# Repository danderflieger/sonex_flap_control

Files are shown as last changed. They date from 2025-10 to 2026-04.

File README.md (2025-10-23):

# Sonex Flap Control
This is an experimental ameteur built (EAB) electronic project that was designed for flap movement and position tracking in my Sonex B model aircraft kit. It uses an Arduino Nano in conjunction with an BTS7960/IBT_2 H-type motor driver to move the Sonex-supplied Electric Flap Actuator (Sonex part SNB-C05-11) and displays current flap position on a small OLED screen. Feel free to use it for your own purposes AT YOUR OWN RISK. It is released under MIT open source agreement license (see the license agreement listed in the root of the project). 

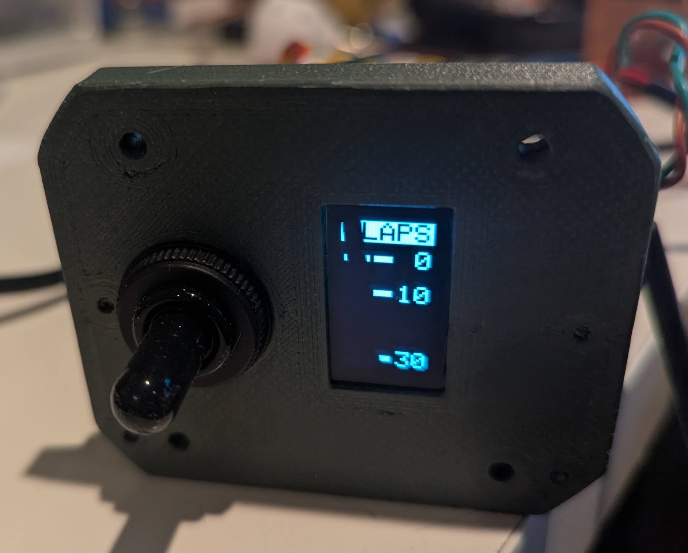
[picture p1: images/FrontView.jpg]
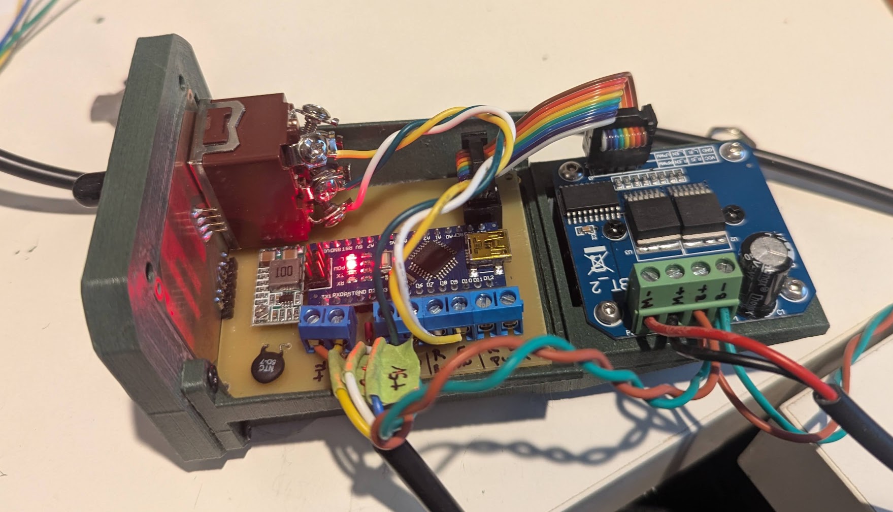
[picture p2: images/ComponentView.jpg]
  

Multiple "notches" can be configured in software. By default, I have added 3 notches - 0 degrees, 10 degrees, and 30 degrees. Pressing the switch upward on the face triggers the arduino to retract the flaps to the previous notch. Pressing down the switch triggers the flaps to extend to the next notch. If the user presses the opposite direction, the flaps stop. However, if the pilot flips the switch in the opposite direction and holds it for more than half a second, the flaps will stop for the half second and then reverse to the next notch. The OLED screen updates constantly to notify the pilot of the current flap position. So if a builder decided to wire the switch directly to the flap actuator, the OLED screen will still keep track of the current position of the flaps, but the pilot would need to hold the switch until the flaps extend/retract to the desired position.

The code has more comment blocks than actual code describing what is happening. Pretty much every line or function has a very detailed description of what it does and what to change (if anything).

For example, after building the device it will need to be calibrated to work with your individual flap actuator (e.g. position readings are likely to be close between your flap actuator and mine, but are unlikely to be __*exactly*__ the same as mine). There is a line of code that you will want to uncomment to view the position reading on the Serial Monitor when the flaps are fully retracted and fully extended (see example below). Those values need to be entered into the code so the device can be sure to reach its __*full range*__ with your actuator. All of that is described in comment blocks in the code. Here's a sample of my comment blocks within the Arduino code file:

```
...

/**************************************************************************
These two values represent the values recevied on the A2 pin of the Arduino,
which is connected to the yellow wire of the position sensor of the flap
actuator. To calibrate your actuator, set the CALIBRATION_OUTPUT to true
and find the sensor reading that appears when  you retract/extend the flap 
actuator to its limits in both directions. Use whatever value appears in
the Serial Monitor to set the FULL_RETRACT_VALUE and FULL_EXTEND_VALUE 
settings here. Then turn off the CALIBRATION_OUTPUT by setting it to false.
No need to continue to output values to the Serial port when it's not
necessary. 
**************************************************************************/
#define FULL_RETRACT_VALUE  5
#define FULL_EXTEND_VALUE   881

/**************************************************************************
 Decide whether or not to output serial data and/or calibration data over
 the serial port (e.g. through the Arduino IDE's Serial Monitor). The 
 SERIAL_OUTPUT switch will output lots of (possibly) useful data. 
 
 If CALIBRATION_OUTPUT is set to true, it will output readings so you can 
 adjust the two values above to match the flap acutator's readings when
 it's extended/retracted fully. 
 
 It's recommended that you set the FULL_RETRACT_VALUE to 0 and the 
 FULL_EXTEND_VALUE value to 1023 to start. Then set the CALIBRATION_OUTPUT 
 value to true and retract the actuator all the way.

 The output in the Serial Monitor will tell you what to put into the 
 FULL_RETRACT_VALUE. Then extend it all the way to figure out what the 
 FULL_EXTEND_VALUE should be set to. 
**************************************************************************/
#define SERIAL_OUTPUT       false
#define CALIBRATION_OUTPUT  false

...

```

The entire code base looks similar to this, with explainations for everything that's going on. If you're not a developer, reading through the comments can help you cut your teeth on Arduino C++ coding. 

# Parts/Supplies List
Here's a list of the parts I used while prototyping. You can probably find other vendors, but your mileage will likely vary. 
### Free-standing parts
  * __Sonex Electric Flap Actuator__
The Electric Flap Actuator requires a feedback circuit. Not all Sonex Electric Flap Actuators had the feedback circuit. To verify that yours has one, you will need to look at the two sets of wires coming out of the actuator. One of them will have a red and black wire - this is for 12-24V power. The other set of wires will have three leads - blue, white, and yellow. 
  * __Arduino Nano__ (https://www.amazon.com/dp/B07G99NNXL)
  * __BTS7960/IBT_2 H-Bridge DC Motor Driver__ (https://www.amazon.com/dp/B099N8XS5P)
  * __.96 inch OLED I2C Display Module - 128x64 pixels__ (https://www.amazon.com/dp/B09T6SJBV5)
  * __Marine-grade heavy duty 12V ON-OFF-ON momentary toggle switch__ (https://www.amazon.com/dp/B0F9P9L9G6)

### PCB-related Parts
Custom Printed Cirtuit Boards are required for this project. For the prototype, I used my ancient Canon laser printer to print a mirrored image on special paper, an iron to transfer the toner to a blank single-sided 
  * __FR-4 Copper Clad PCB Laminate, Single Side, 4x2.7 inch__ (https://www.amazon.com/dp/B01MCVLDDZ)
  * __Voltage Reducer/Buck Converter (set to 9V output)__ (https://www.amazon.com/dp/B08JZ5FVLC)
  * __PCB Screw Terminal Blocks__ (https://www.amazon.com/dp/B014GMRBH2) 
  * __Straight AND Right Angle 2.54mm Male Header Pins__ (https://www.amazon.com/dp/B0CN14TP2T)
  * __2x4 8P 2.54mm Straight Male Shrouded PCB Box Header IDC Socket__ (https://www.amazon.com/dp/B08DYFQKB1)

The Socket makes connecting the custom PCB to the motor driver board very simple and clean. You have two choices for the cable - you can buy the components and make your own custom cable (which is what I did) or you can purchase one already complete. I opted to make my own because the pre-made ones are a little too long and I didn't like that. 
  * __(pre-made) 2x4 Ribbon Cable__ (https://www.amazon.com/dp/B07DFBPZLJ)
  * __(custom) 2x4 FC-8P 2.54mm Dual Rows IDC Sockets Female Connector for Flat Ribbon Cable__ (https://www.amazon.com/dp/B0BVHMTY5S)
  * __(custom) Flat Ribbon Cable for 2.54mm 0.1" Spacing Connectors__ (https://www.amazon.com/dp/B0762ZCRYN)

### Other Recommended Parts
  * __Ferrule Crimping Tool and Connectors - crimp ends of wires to reduce fatigue__ (https://www.amazon.com/dp/B0DRJ9CDNG)
  * __22 AWG Stranded Tinned Copper Wire with Silicone Insulation__ (https://www.amazon.com/dp/B0881HCN37)

# Wiring
There are two sets of wires coming out of the Electronic Flap Actuator. One set is for powering the motion of the Actuator and the other set is for reporting its position.

### Power Wires

While the actuator has a red and a black wire coming out of it for motion, they won't always be positive/negative. If you give the red wire +12V and the black wire -12V, it will extend. If you reverse the polarity (+12V to black and -12V to red) the actuator will retract:
  * 🔴 RED:   Power (+ to extend, - to retract)
  * ⚫ BLACK: Power (- to extend, + to retract)

That said, there are two options for how to wire up the power to the actuator:

* You can wire the actuator to directly use 12/24V with a 6-pole, ON-OFF-ON momentary switch wired up like this (I got this diagram from an email sent to me by Sonex Support). This requires the pilot to press and hold the switch until the flaps reach the desired position:

  

* -OR- You can use the motor driver to change the polarity of the actuator for you. In this case, the motor controller is controlled by the Arduino and programmed to move the actuator in notches - so the pilot just flips and releases the switch in the direction the flaps should go for literally a few milliseconds - no need to hold it - and then goes back to flying the airplane while the flaps move to the desired position with no additional input required from the pilot.

Both of these options will work with the indicator, requiring no change to the code. The Arduino will listen for switch input, but if no pilot input is received, it just merrily skips to the position reading and diplays it on the little screen. 

#### Motor Driver Use Discussion
The motor driver has several inputs and two outputs. The two outputs are the red and black wires on the actuator. The motor driver will determine how much voltage (and which polarity - remember we need to reverse the polarity to the actuator for retraction) to push to the actuator based on the other pins. Here's a list of the other pins and what they do:

* __M-__ - Output to the Actuator (this will output positive or negative power, depending on which way the actuator should move)
* __M+__ - Other output to the Actuator (this will output negative or positive power, depending on which way the actuator should move)
* __B-__ - This is the max negative power source/ground of the airplane 
* __B+__ - This is the max positive power (e.g. +12V from the battery) that can be pushed to the actuator. The Motor Driver can handle up to 36V, but I suggest just using the common 12V or 24V.
* __VCC__ - This is 5V provided by the Arduino. It's only used to power the LOGIC of the motor driver (not the motor itself)
* __GND__ - This is a common ground between the Arduino and the Motor Driver
* __R_IS__ and __L_IS__ - These two pins are not used in this project - I think they're for re-programming the motor driver or something like that. Just ignore them.
* __R_EN__ and __L_EN__ - These two pins are given 5V, which "enables" the two BTS7960 chips (one is on the right and one is on the left). If these pins are not "enabled" with 5V, the motor driver won't send any power to the Actuator
* __RPWM__ and __LPWM__ - These two pins are controlled by the Arduino - one for each BTS7960 chip on the Motor Driver board. Depending on the PWM signal from the arduino on either of these two pins, the motor driver will send a variable voltage to the actuator. To extend, we give a high PWM to the RPWM pin and NO signal to the LPWM pin. To retract, we give a high PWM signal to the LPWM pin and NO signal to the RPWM pin. see below for a description of PWM.

#### PWM Discussion
Pulse Width Modulation (PWM) is determined by turning a signal pin on and off at varying rates. Arduinos are designed to do this on their digital pins. We can set a PWM value between 0 and 255 on any Arduino digital pin. A PWM cycle is the amount of time in which a pin goes from on to off. Each PWM cycle on a typical Arduino (such as the Nano used in the project), that cycle is about every 2 milliseconds. 

A PWM value of 0 denotes that the pin is always outputting 0V. A PWM of 255 denotes that the pin
is always outputting 5V. 

A PWM output of 127 means that a pin is on (5V) for about 1ms and off (0V) for about 1ms. 

A PWM of 63 (half of 127) means that the pin will be turned on (5V) for 500 micro seconds (half of a millisecond) and off (0V) for 1500 microseconds (1.5 milliseconds). Or in other words, for about 1/4 of the cycle the pin will be outputting 5V and the other 3/4 of the cycle it will be outputting 0V.

To tell the Motor Driver to move the actuator in one direction or the other, you need to send two PWM signals - one to each of the BTS7960 chips. 

To extend the actuator, we would send a PWM of 0 to the RPWM pin and a PWM of 255 to the LPWM pin on the motor driver. This will cause the output terminal to push +12V to the red wire and -12V to the black wire on the actuator. 

To retract the actuator, we do the opposite. E.g. send a PWM of 0 to the LPWM pin and a PWM of 255 to the RPWM pin on the driver. This will revers the polarity to the actuator +12V on the BLACK wire and -12V on the RED wire. 

To slow down the motion of actuator, you would set your PWM signal at a low number - say 10. 

To speed up the movement of the actuator, you would increase the PWM to something higher - 1 to 255. 

There's a good write-up on Arduino's website about PWM - it's worth reading:
https://docs.arduino.cc/learn/microcontrollers/analog-output/ 

Note: For this project, there's no danger in just telling the motor controller to move in one direction at full speed until it reaches it's desired flap position. The actuator moves slowly enough to not worry about overshooting your flap setting by very much - I've added an additional threshold variable to account for the actuator "coasting" momentarily after telling it to stop. If set properly, this threshold will stop the actuator exactly where you want it to stop.

Now, on to the other set of wires coming out of the Electronic Flap Actuator ...

### Position Sensor Wires

The real benefit to this project is the flap position indicator. You can use the built-in position sensor to display the position of the flaps on your panel.

  * 🔵 BLUE: +5V
  * ⚪ WHITE: -5V/Ground
  * 🟡 YELLOW: 0 to +5V Signal wire (read by analog pin A2 on Arduino)

Every time the Arduino loops through the aptly named loop() function, it checks to see if there's any input from the pilot (if so, it tries to do what the pilot told it to do) and it also takes a reading from the sensor wires and updates the OLED screen with the new reading. This happens hundreds of times per second and gives near instant updates on the little screen. 

#### How the position sensor works
The position sensor is fed +5V on the blue wire and -5V on the white wire. There's a potentiometer in between with an output (yellow wire) that will output anywhere from 0V (if fully retracted) to +5V (if fully extended). If it's roughly halfway between the two, the yellow wire will output about +2.5V. 

One of the Arduino's analog pins (in this case A2) is set up to listen to the amount of voltage coming through that yellow wire. It then translates that voltage to a number between 0 and 1023. In the code, we then use a "map()" function to interpolate the value from a min/max range that the pin can read (0-1023) to a range that makes sense from a "degrees of flaps" perspective (this is defined in the code 0-30, but can be eaily changed to something else). The map() function works like this:

```
map([value recevied from yellow wire - 0-1023], [min input value - e.g. fully retracted reading], [max input value - e.g. fully extended reading], [min flap angle as defined], [max flap angle as defined]); 
```

So, given that:

* our sensor is currently sending 2.5V to the Arduino, so the Arduino reads __511__ (half way between 0 and 1023)
* our min/max values that the sensor outputs (say 0 to +5V) is converted to a number between __0__ and __1023__
* our min/max angle settings are __0__ and __30__  

that means our map() function would look like this:

__flapAngle = map(511, 0, 1023, 0, 30);__

In this case, the flapAngle variable would be set to 15 degrees of flap (e.g. half way between 0 and 30, because the actuator's sensor is reporting that it's halfway between fully extended and fully retracted). 

Once we have that value, we use a handy little OLED library written by the folks at Adafruit to draw a little rectangle on the left half of the screen (showing graphically where the flaps are currently positioned) next to a previously drawn set of lines and numbers showing where certain values will appear on the screen (on the right). 

Incedentally, we use another map() function to convert the angle value we figured out a minute ago to determine where to place the little rectangle based on the number of pixels high the screen is, minus the text at the top that says FLAPS. Giving similar values, our map() function to find the vertical position of our rectangle would look like this (where the range of available pixels is 8 to 128):

rectangleTopLeftCorner = (15, 0, 30, 8, 128); 

So the rectangleTopLeftCorner variable would be set to 60 - which means the rectangle's top left corner would be drawn on the screen at 60 pixels from the top. map() is a very handy little function!

Anyway, that's a pretty good intro. For more details, go read the comment blocks in the code - I explain a lot more there.

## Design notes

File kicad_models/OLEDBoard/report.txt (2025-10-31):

Plotted to 'C:\Users\ripperuser\Documents\sonex_flap_control\kicad_models\ArduinoBoard\GerberFiles\ArduinoBoard-F_Cu.gbr'.
Plotted to 'C:\Users\ripperuser\Documents\sonex_flap_control\kicad_models\ArduinoBoard\GerberFiles\ArduinoBoard-B_Cu.gbr'.
Plotted to 'C:\Users\ripperuser\Documents\sonex_flap_control\kicad_models\ArduinoBoard\GerberFiles\ArduinoBoard-F_Paste.gbr'.
Plotted to 'C:\Users\ripperuser\Documents\sonex_flap_control\kicad_models\ArduinoBoard\GerberFiles\ArduinoBoard-B_Paste.gbr'.
Plotted to 'C:\Users\ripperuser\Documents\sonex_flap_control\kicad_models\ArduinoBoard\GerberFiles\ArduinoBoard-F_Silkscreen.gbr'.
Plotted to 'C:\Users\ripperuser\Documents\sonex_flap_control\kicad_models\ArduinoBoard\GerberFiles\ArduinoBoard-B_Silkscreen.gbr'.
Plotted to 'C:\Users\ripperuser\Documents\sonex_flap_control\kicad_models\ArduinoBoard\GerberFiles\ArduinoBoard-F_Mask.gbr'.
Plotted to 'C:\Users\ripperuser\Documents\sonex_flap_control\kicad_models\ArduinoBoard\GerberFiles\ArduinoBoard-B_Mask.gbr'.
Plotted to 'C:\Users\ripperuser\Documents\sonex_flap_control\kicad_models\ArduinoBoard\GerberFiles\ArduinoBoard-Edge_Cuts.gbr'.
Created Gerber job file 'C:\Users\ripperuser\Documents\sonex_flap_control\kicad_models\ArduinoBoard\GerberFiles\ArduinoBoard-job.gbrjob'.
Info: Done.
Plotted to 'C:\Users\ripperuser\Documents\sonex_flap_control\kicad_models\ArduinoBoard\GerberFiles\ArduinoBoard-F_Cu.gbr'.
Plotted to 'C:\Users\ripperuser\Documents\sonex_flap_control\kicad_models\ArduinoBoard\GerberFiles\ArduinoBoard-B_Cu.gbr'.
Plotted to 'C:\Users\ripperuser\Documents\sonex_flap_control\kicad_models\ArduinoBoard\GerberFiles\ArduinoBoard-F_Paste.gbr'.
Plotted to 'C:\Users\ripperuser\Documents\sonex_flap_control\kicad_models\ArduinoBoard\GerberFiles\ArduinoBoard-B_Paste.gbr'.
Plotted to 'C:\Users\ripperuser\Documents\sonex_flap_control\kicad_models\ArduinoBoard\GerberFiles\ArduinoBoard-F_Silkscreen.gbr'.
Plotted to 'C:\Users\ripperuser\Documents\sonex_flap_control\kicad_models\ArduinoBoard\GerberFiles\ArduinoBoard-B_Silkscreen.gbr'.
Plotted to 'C:\Users\ripperuser\Documents\sonex_flap_control\kicad_models\ArduinoBoard\GerberFiles\ArduinoBoard-F_Mask.gbr'.
Plotted to 'C:\Users\ripperuser\Documents\sonex_flap_control\kicad_models\ArduinoBoard\GerberFiles\ArduinoBoard-B_Mask.gbr'.
Plotted to 'C:\Users\ripperuser\Documents\sonex_flap_control\kicad_models\ArduinoBoard\GerberFiles\ArduinoBoard-Edge_Cuts.gbr'.
Created Gerber job file 'C:\Users\ripperuser\Documents\sonex_flap_control\kicad_models\ArduinoBoard\GerberFiles\ArduinoBoard-job.gbrjob'.
Info: Done.
Info: Done.
Info: Done.

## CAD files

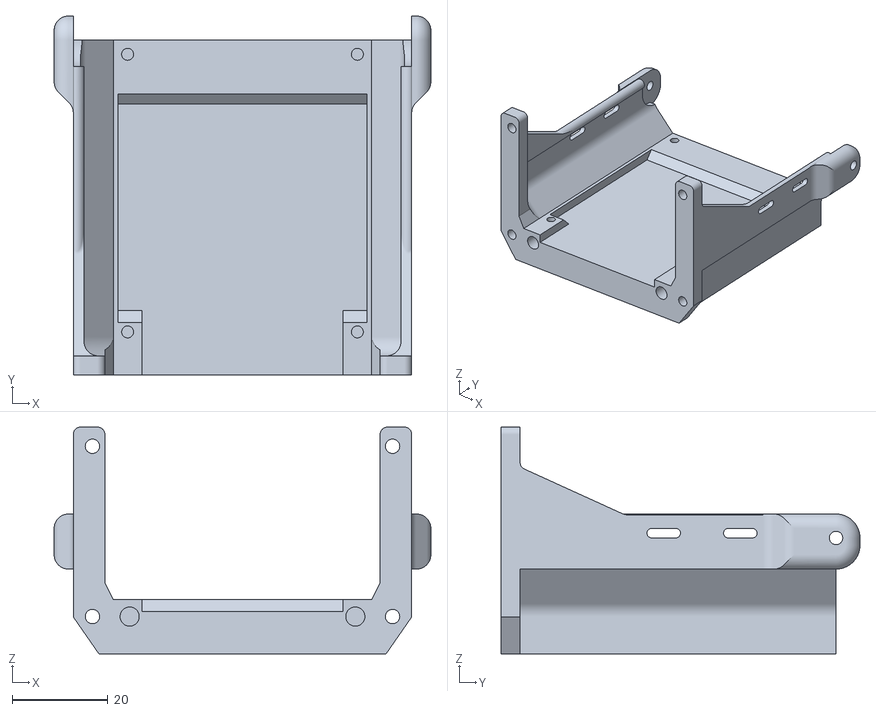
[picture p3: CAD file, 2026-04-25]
Solid Edge/STL Files/MainBoardBed.stl
78.7 x 75.0 x 47.4

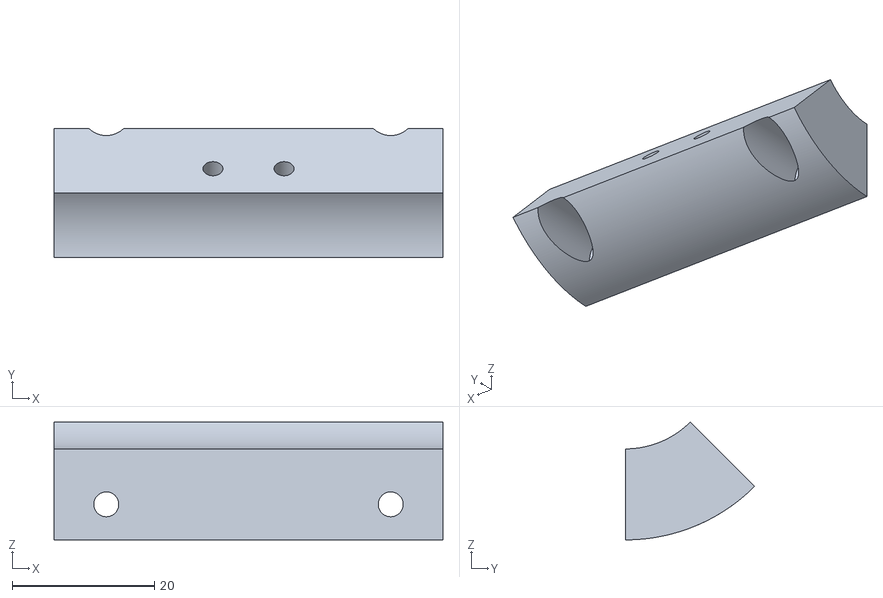
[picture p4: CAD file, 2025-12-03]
Solid Edge/STL Files/45DegMotorBoardBedSpacer.stl
54.7 x 18.1 x 16.6

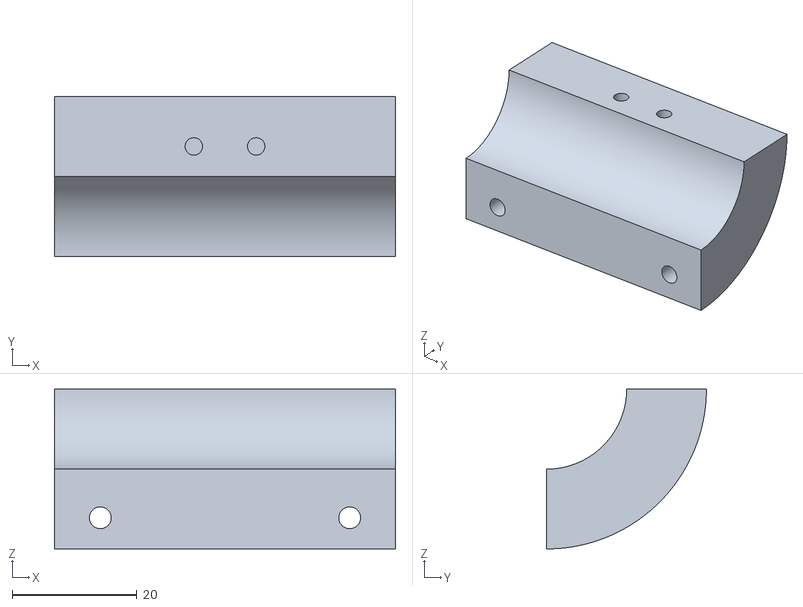
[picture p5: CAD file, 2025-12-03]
Solid Edge/STL Files/90DegMotorBoardBedSpacer.stl
54.7 x 25.6 x 25.6

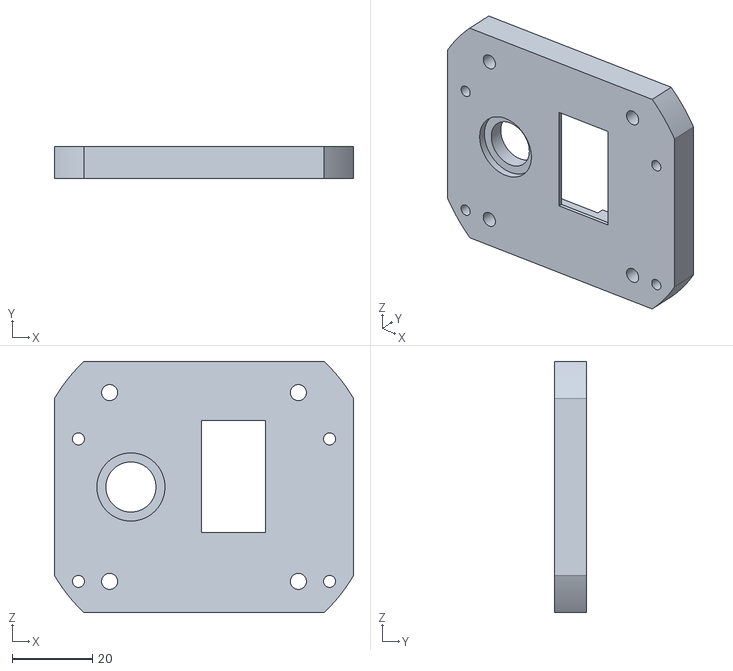
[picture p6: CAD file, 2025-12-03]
Solid Edge/STL Files/FacePlate.stl
74.7 x 8.00 x 62.7

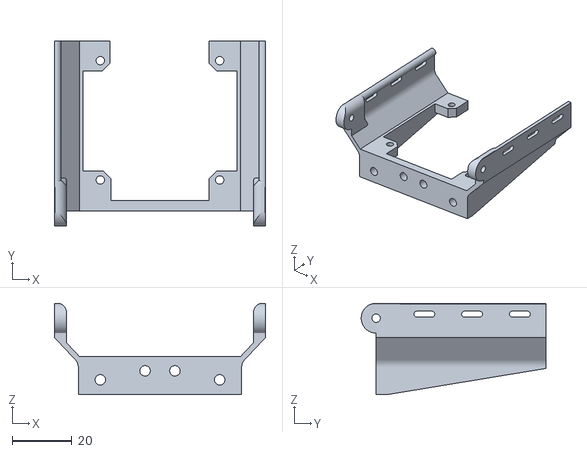
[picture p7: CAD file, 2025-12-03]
Solid Edge/STL Files/MotorDriverMount.stl
70.7 x 61.9 x 30.6

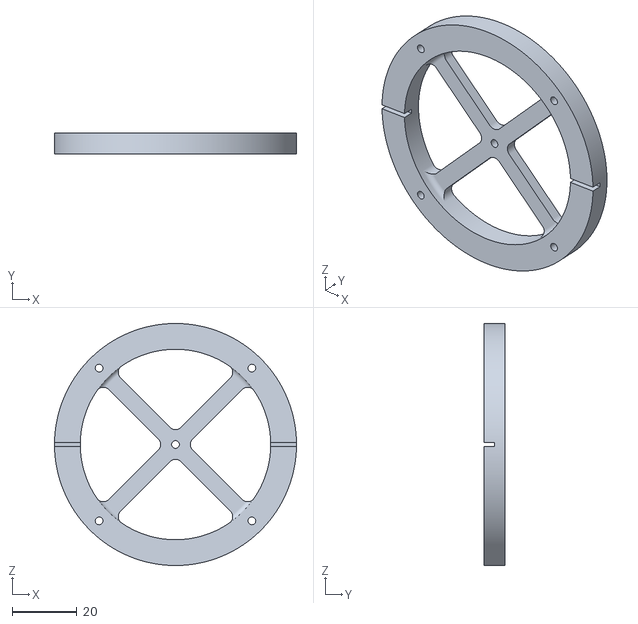
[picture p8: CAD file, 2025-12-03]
Solid Edge/STL Files/Panel Hole Template.stl
74.7 x 6.35 x 74.7

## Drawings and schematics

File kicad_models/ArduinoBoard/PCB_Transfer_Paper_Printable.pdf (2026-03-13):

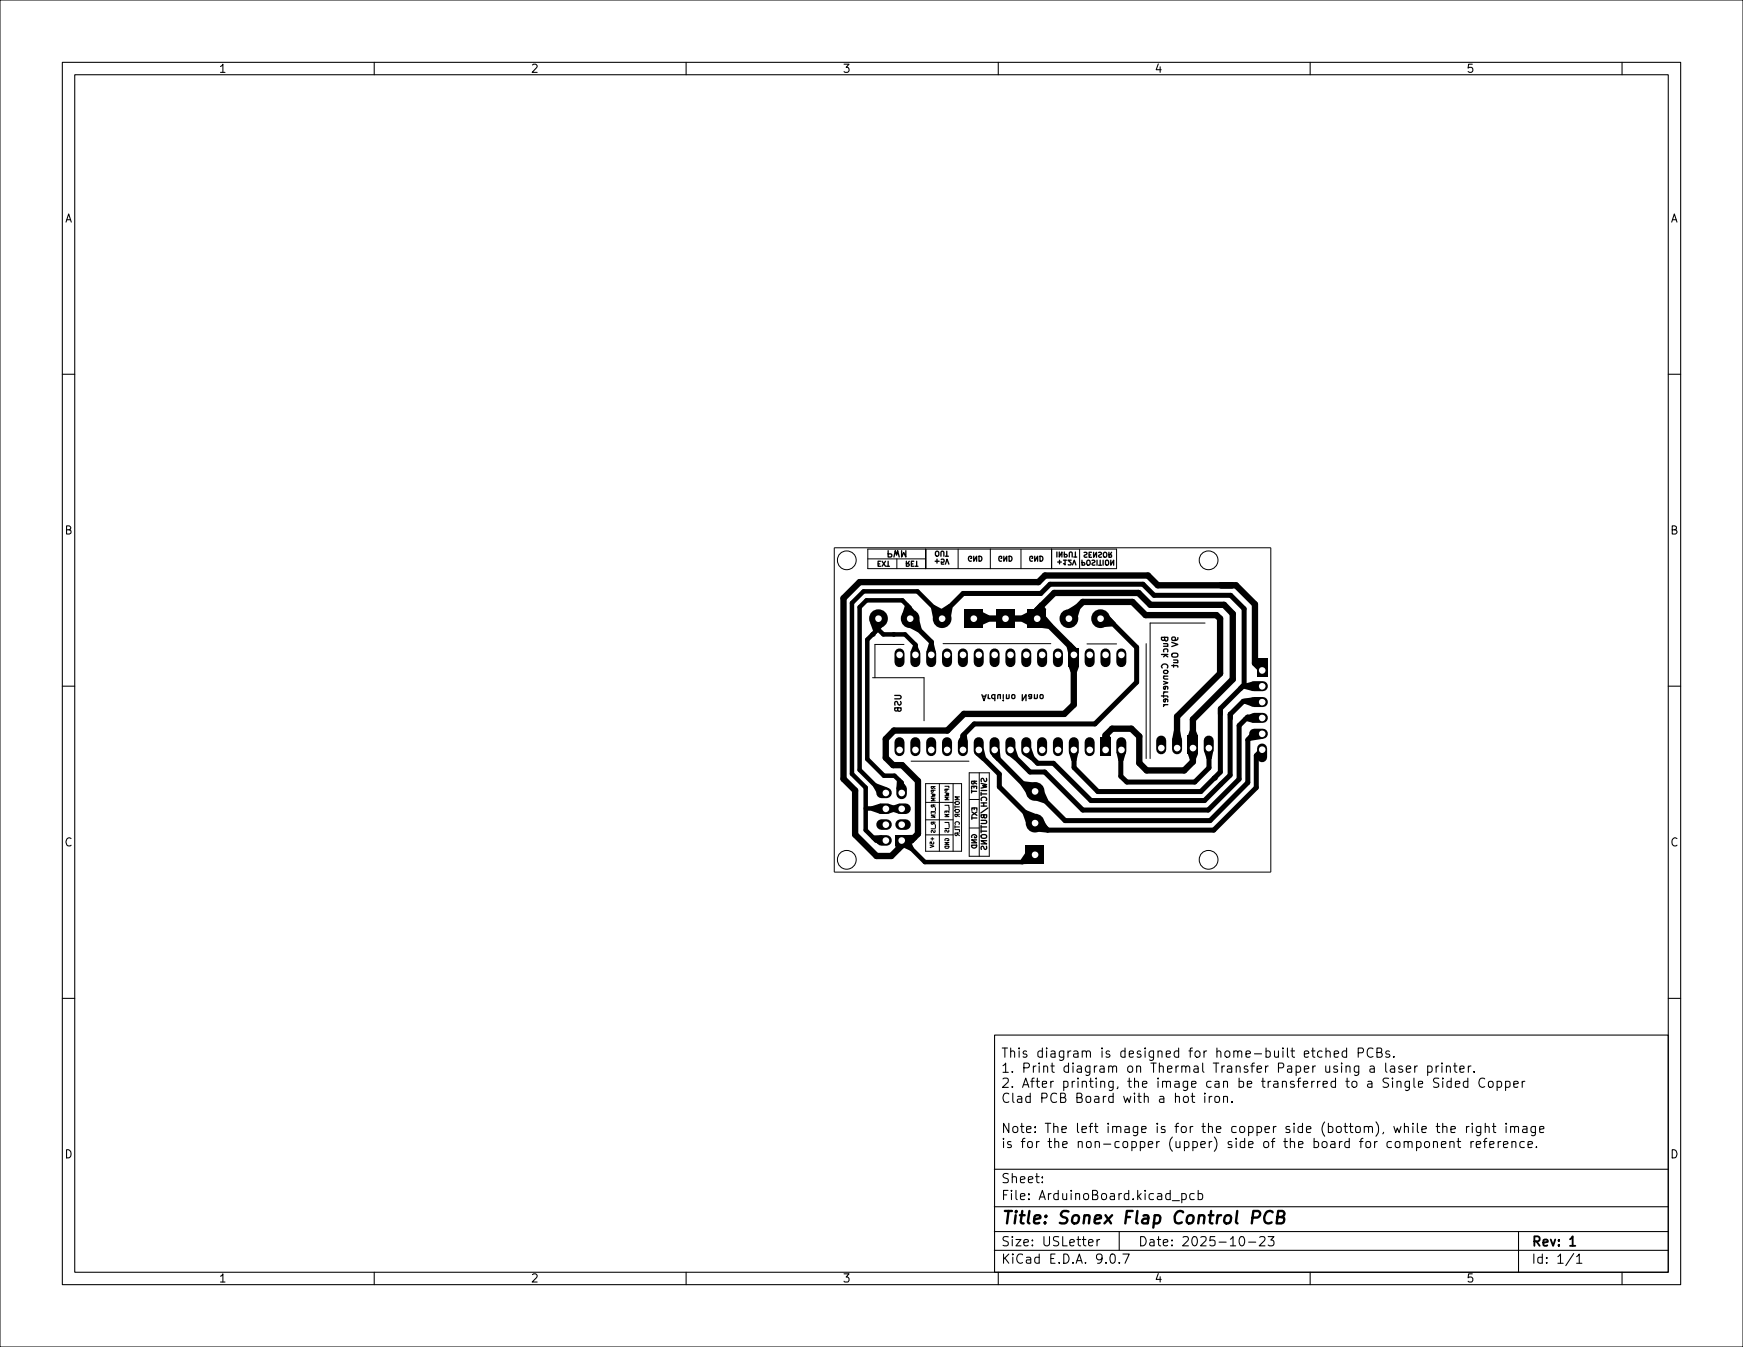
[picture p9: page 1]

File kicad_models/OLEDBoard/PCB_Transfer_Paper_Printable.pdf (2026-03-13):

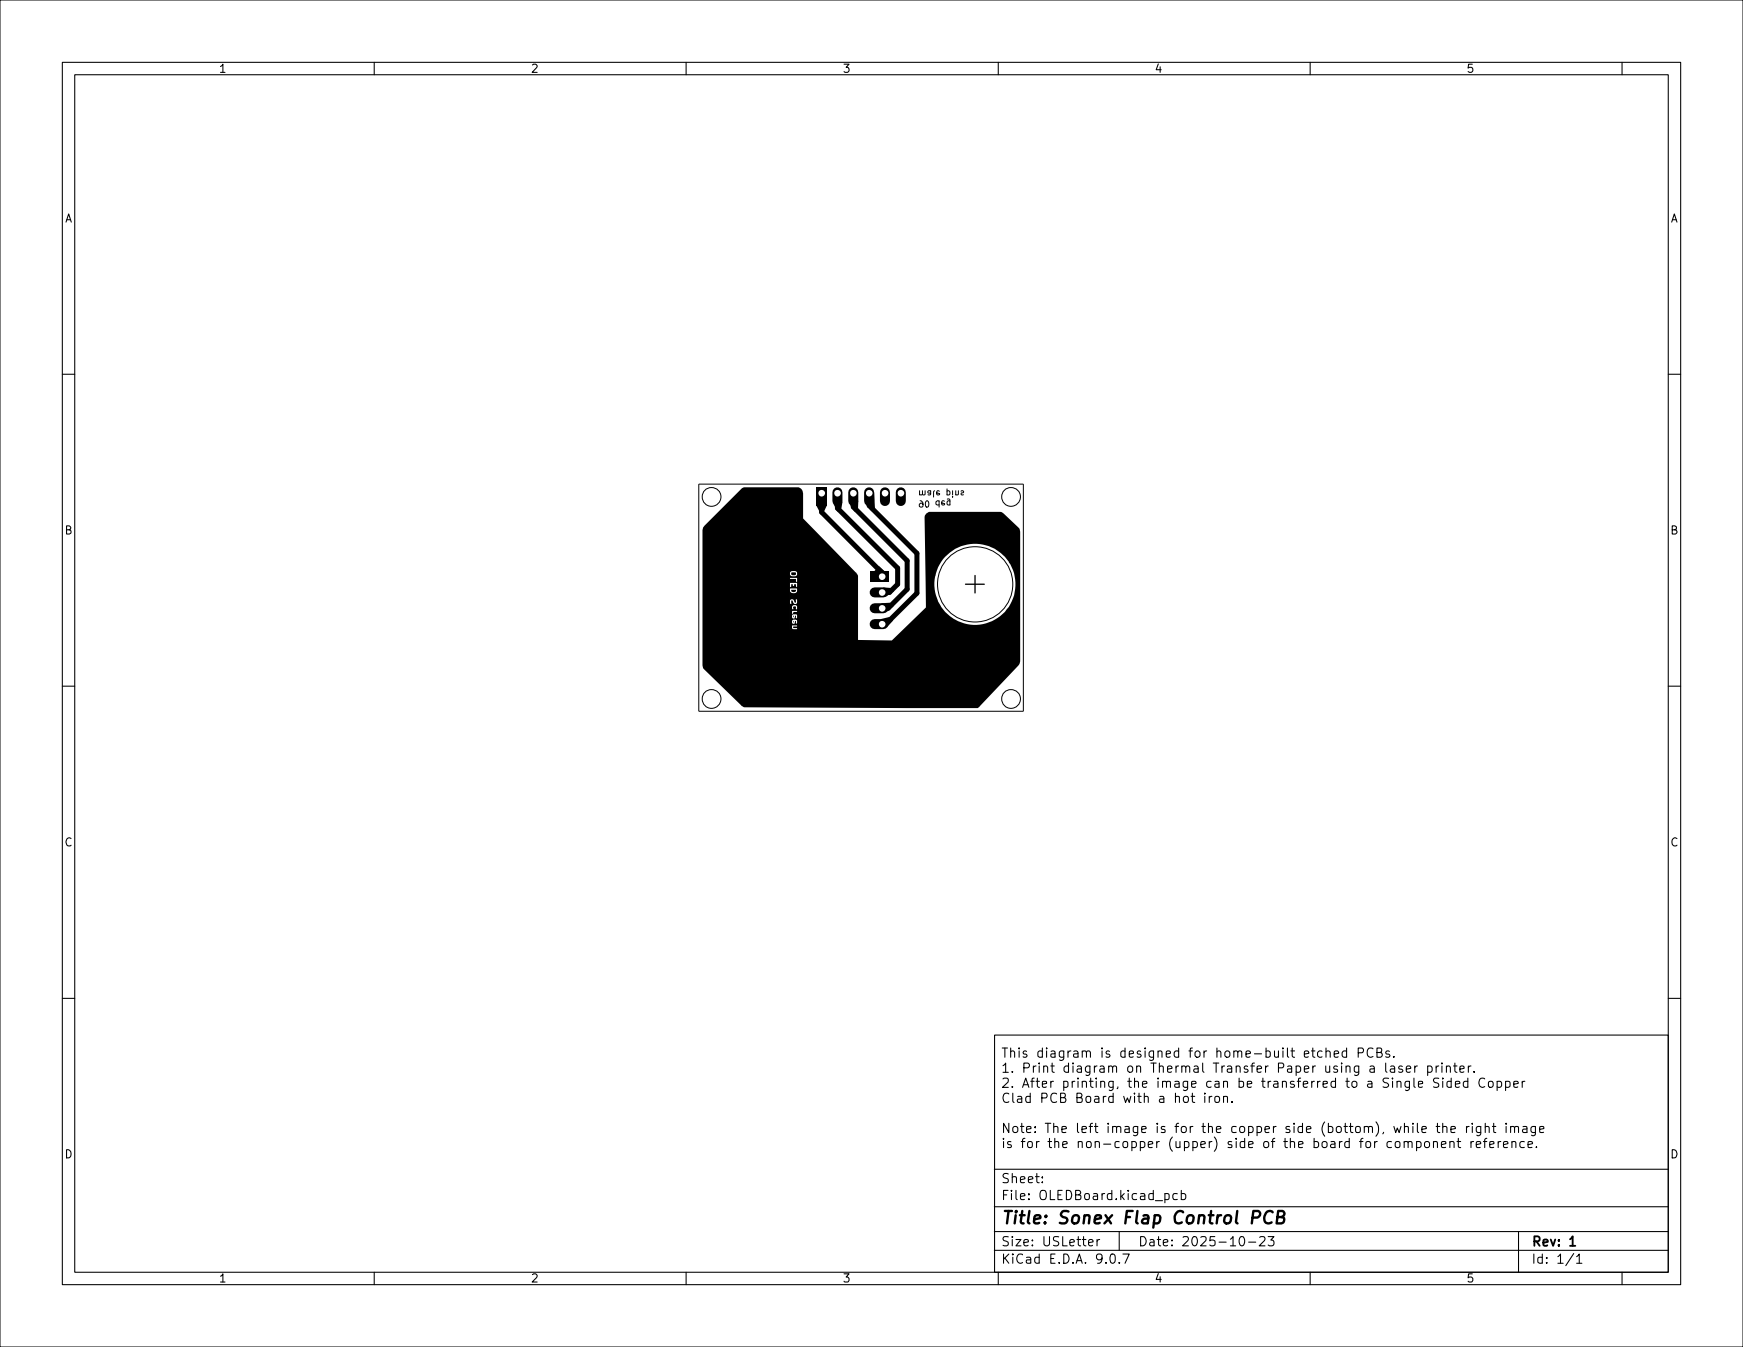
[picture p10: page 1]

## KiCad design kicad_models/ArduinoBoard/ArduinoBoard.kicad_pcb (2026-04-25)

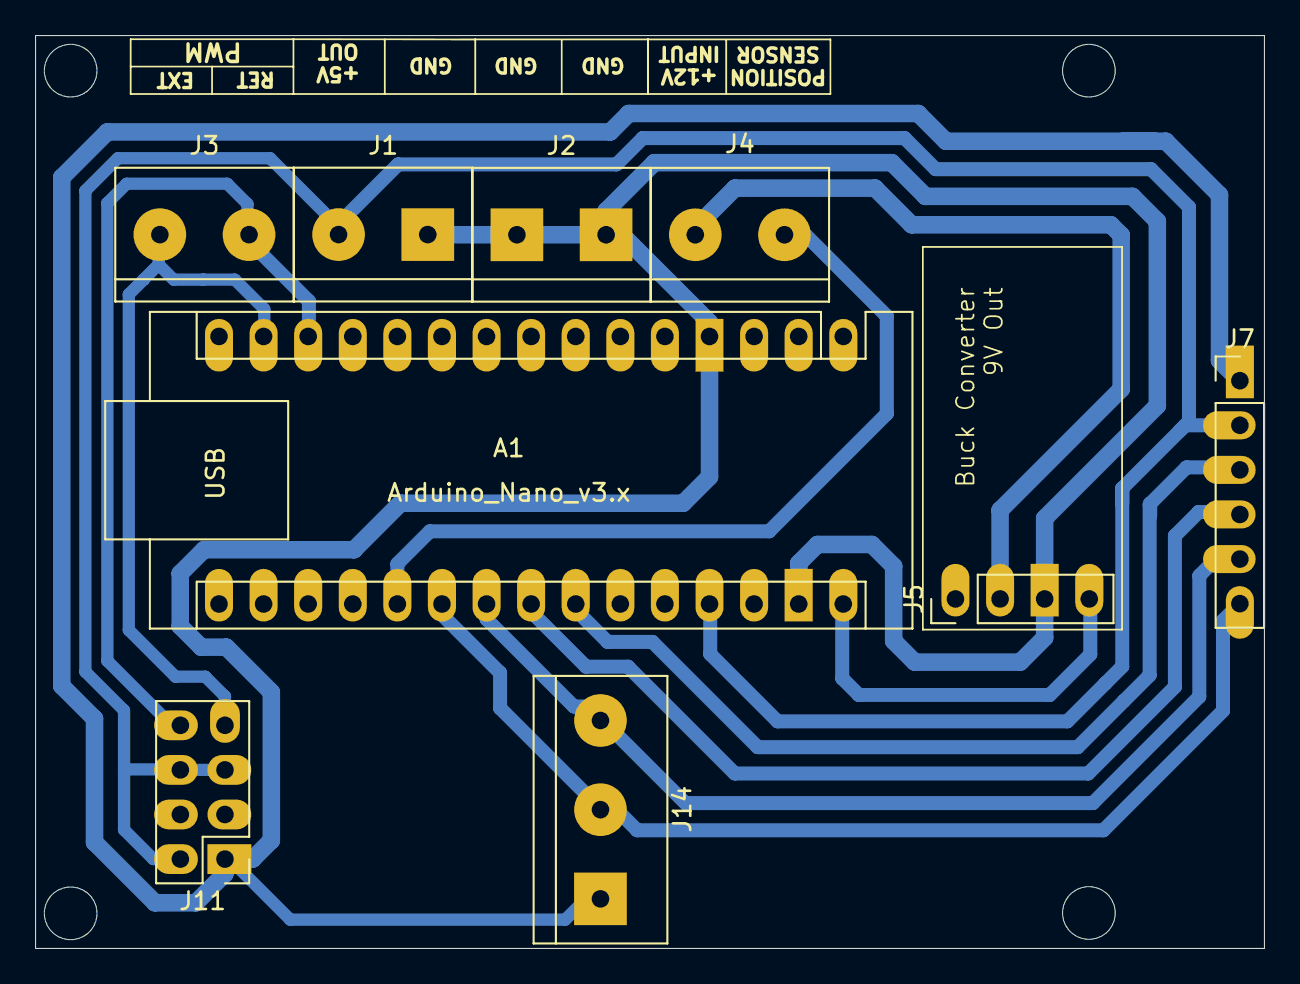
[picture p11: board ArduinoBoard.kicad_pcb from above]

Board: 2 copper layers, 70.0 x 52.0 mm, 9 parts (0 on the bottom side), 11 nets.

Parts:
A1: Arduino_Nano_v3.x; Arduino_Nano
J1, J2: 5V Output; TerminalBlock_bornier-2_P5.08mm
J3: PWM Output; TerminalBlock_bornier-2_P5.08mm
J4: 12V Input; TerminalBlock_bornier-2_P5.08mm
J5: Conn_01x04_Pin; PinHeader_1x04_P2.54mm_Vertical
J7: Conn_01x06_Pin; PinHeader_1x06_P2.54mm_Vertical
J11: Conn_02x04_Odd_Even; PinHeader_2x04_P2.54mm_Vertical
J14: Switch/Buttons; TerminalBlock_bornier-3_P5.08mm

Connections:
/GND: A1.4 (GND), A1.29 (GND), J1.2, J2.1, J2.2, J5.3, J7.1, J11.1, J14.3
/VI+: J4.1, J5.2
/VO+: A1.30 (VIN), J5.4
unnamed: A1.27 (+5V), J1.1, J7.2, J11.2, J11.5, J11.6
unnamed: A1.20 (A1), J4.2
unnamed: A1.21 (A2), J7.6, J14.2
unnamed: A1.22 (A3), J7.5, J14.1
unnamed: A1.23 (A4), J7.4
unnamed: A1.24 (A5), J7.3
unnamed: A1.13 (D10), J3.2, J11.8
unnamed: A1.14 (D11), J3.1, J11.7

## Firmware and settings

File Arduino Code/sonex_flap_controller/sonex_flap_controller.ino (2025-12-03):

/**************************************************************************
  MIT License

  Copyright (c) 2025 Dan Der Flieger

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
  THE SOFTWARE IS PROVIDED "AS IS", WITHOUT WARRANTY OF ANY KIND, EXPRESS OR
  IMPLIED, INCLUDING BUT NOT LIMITED TO THE WARRANTIES OF MERCHANTABILITY,
  FITNESS FOR A PARTICULAR PURPOSE AND NONINFRINGEMENT. IN NO EVENT SHALL THE
  AUTHORS OR COPYRIGHT HOLDERS BE LIABLE FOR ANY CLAIM, DAMAGES OR OTHER
  LIABILITY, WHETHER IN AN ACTION OF CONTRACT, TORT OR OTHERWISE, ARISING FROM,
  OUT OF OR IN CONNECTION WITH THE SOFTWARE OR THE USE OR OTHER DEALINGS IN THE
  SOFTWARE.
**************************************************************************/


/**************************************************************************
  Include a few necessary libraries - the Adafruit ones need to be installed
  into the Arduino IDE before this will compile. See the copyright info 
  for the Adafruit libraries at the bottom of this file. Basically, just 
  consider the time and money expended to write a freely available library
  and think about buying their hardware (which is top-notch). 
**************************************************************************/
#include <SPI.h>
#include <Wire.h>
#include <Adafruit_GFX.h>
#include <Adafruit_SSD1306.h>


/**************************************************************************
These two values represent the values recevied on the READING_PIN pin of the 
Arduino, which is connected to the yellow wire of the position sensor of the 
flap actuator. To calibrate your actuator, set the CALIBRATION_OUTPUT to 
true and find the sensor reading that appears when  you retract/extend the 
flap actuator to its limits in both directions. Use whatever value appears 
in the Serial Monitor to set the FULL_RETRACT_VALUE and FULL_EXTEND_VALUE 
settings here. Then turn off the CALIBRATION_OUTPUT by setting it to false.
No need to continue to output values to the Serial port when it's not
necessary. 
**************************************************************************/
#define FULL_RETRACT_VALUE  6
#define FULL_EXTEND_VALUE   880


/**************************************************************************
When a sensor reading is taken, because it is an analog sensor, sometimes
the number bounces around a little. For example, say the sensor is reading 
an average of 300. It will likely bounce between 299 and 301. Or maybe a 
range of 297 and 303. The value below (ANTI_FLICKER_VALUE) is used to 
attempt to round down by this many. So if it bounces between 300 and 301, 
it should report 300. 

If you see a lot of bounce, you may need to increase this number to, say, 
3 or 4 (whatever the range of the bounce is). When you do, you may need 
to adjust the two numbers above (FULL_RETRACT_VALUE and FULL_EXTEND_VALUE) 
to be divisible by whatever number you input here. Setting this to a lower 
number (2 by default) will make your reading more accurate, but there's a 
higher chance the bar indicating the current position of your flasp will 
"flicker" between two values. Setting it to a higher number reduces the 
liklihood of flicker, but may be a little less accurate. So weigh the 
importance of each when you set this up. 
**************************************************************************/
#define ANTI_FLICKER_VALUE 4


/**************************************************************************
 Decide whether or not to output serial data and/or calibration data over
 the serial port (e.g. through the Arduino IDE's Serial Monitor). The 
 SERIAL_OUTPUT switch will output lots of (possibly) useful data. 
 
 If CALIBRATION_OUTPUT is set to true, it will output readings so you can 
 adjust the two values above to match the flap acutator's readings when
 it's extended/retracted fully. 
 
 It's recommended that you set the FULL_RETRACT_VALUE to 0 and the 
 FULL_EXTEND_VALUE value to 1023 to start. Then set the CALIBRATION_OUTPUT 
 value to true and retract the actuator all the way.

 The output in the Serial Monitor will tell you what to put into the 
 FULL_RETRACT_VALUE. Then extend it all the way to figure out what the 
 FULL_EXTEND_VALUE should be set to. 
**************************************************************************/
#define SERIAL_OUTPUT       false
#define CALIBRATION_OUTPUT  true


/*************************************************************************
  These values are used to determine how long the system waits with no movement 
  before it stops trying to move the flaps. For example, when the flaps reach 
  full retraction or extention values, but haven't quite met the FULL_RETRACT_VALUE 
  or FULL_EXTEND_VALUE threshold - the Arduino will continue to send PWM values to
  the motor driver. However, there is a safety switch in the actuator that 
  cuts power to the actuator motor. So the Arduino will sit in a state where
  it's attempting to move the actuator, but it's not moving. These values will
  only allow the PWM signals to continue without movement for a certain number
  of milliseconds (default = 500 or half a second) before changing to DIRECTION_STOP.
*************************************************************************/
#define MAX_IDLE_TIME 500


/*************************************************************************
  This value can be adjusted to allow the actuator to stop slightly before
  it reaches a specific notch. It helps to ensure the actuator doesn't 
  go past the target as it slows - e.g., the Arduino will tell the 
  actuator to stop moving slightly before it reaches the target setting.
  Increase this number to stop it sooner. Decrease it to stop it later. 
  Note that this number MUST be positive - negative numbers don't work 
  properly.
*************************************************************************/
#define TARGET_TOLERANCE 5


/**************************************************************************
This is where you define your various flap notches. You can pretty much
put any integer values you want to appear on the screen - BUT THEY MUST
BE IN NUMERICAL ORDER!! 

Ideally you will do some testing to figure out what angles your flaps actually
sit at for each notch. The first and last element in this array should be 0 and 
whatever full flaps are deflected to. Sonex says full flaps on the B model is 
30 deg. Because they suggest 0 for clean, 10 for takeoff, and 30 for landing, 
that's what I've put here:

int ANGLES[] = { 0, 10, 30 };

Feel free to add additional "notches" in there if you think it's necessary. 
If you wanted to add a notch for 20 deg (for example), it would look like this:

int ANGLES[] = { 0, 10, 20, 30 };
***************************************************************************/ 
int ANGLES[] = { 0, 10, 30 };


/**************************************************************************
 This figures out the number of notches for later use - nothing to change 
 here. It will figure out how many notches you defined based on the ANGLES[] 
 values you entered above. 
**************************************************************************/
#define NOTCH_COUNT sizeof(ANGLES) / sizeof(ANGLES[0])


/**************************************************************************
  Declare another array with similar values. The difference here is that this
  array will hold actual sensor readings, not angles. Because sensor readings 
  have a larger range (e.g. 0-1023 instead of 0-30 degrees), we can start 
  and stop the actuator with better precision. I had an issue where I would 
  target, say, 20 degrees of flap, but the actuator would "coast" to 21 or
  22 degrees before it stopped. And when retracting, it would go to 19 or 18
  degrees before stopping. This is meant to fix that by triggering it to stop
  fractionally sooner, but I needed better precision than what ANGLES can 
  provide. 
**************************************************************************/
int SENSOR_READINGS[NOTCH_COUNT];

/************************************************************************** 
Declare and initialize (to 0) a few variables that are used in the program
***************************************************************************/ 
int           CURRENT_NOTCH         = 0;
int           TARGET_NOTCH          = 0;
int           LAST_SENSOR_READING   = 0;
unsigned long LAST_MOVEMENT_MILLIS  = 0;


/***************************************************************************
 a couple of pre-defined values (enums) that determine which way the flaps 
 should move (or not)
***************************************************************************/ 
#define DIRECTION_RETRACT -1
#define DIRECTION_STOP 0
#define DIRECTION_EXTEND 1


/***************************************************************************
 Define a public variable to define the current direction of the actuator - 
 0:DIRECTION_STOP, 1: DIRECTION_EXTEND, -1: DIRECTION_RETRACT
 This value will be used to determine if the actuator should be moving in one direction or
 the other (or stop) between button presses until it has reached the specified notch
***************************************************************************/ 
int MOTION_DIRECTION = DIRECTION_STOP;


/***************************************************************************
 Define some values for the OLED screen and utilize the Adafruit SSD1306 
 OLED library to configure the OLED screen
***************************************************************************/
#define TITLE_MARGIN    8
#define TITLE_HEIGHT    20
#define SCREEN_WIDTH    128
#define SCREEN_HEIGHT   64
#define OLED_RESET      -1 // Reset pin # (or -1 if sharing Arduino reset pin)
#define SCREEN_ADDRESS  0x3C ///< See datasheet for Address; 0x3D for 128x64, 0x3C for 128x32
Adafruit_SSD1306 display(SCREEN_WIDTH, SCREEN_HEIGHT, &Wire, OLED_RESET);


/***************************************************************************
 define pin numbers for reading and buttons
***************************************************************************/
#define READING_PIN     A1
#define RETRACT_BUTTON  A2
#define EXTEND_BUTTON   A3


/***************************************************************************
Define pin numbers and speed for Pulse Width Modulation (PWM), which is used to tell 
the motor driver to move at a certain speed or stop.

In case you don't know what PWM is ... 

The first two lines below define which of the Arduino's digital pins are to be used for
PWM signalling (pins 10 and 11). They are both "digital" pins, meaning they can only be 
either on or off (nothing in between).

PWM is determined by turning each of the pins on and off at a set rate, from 0-255. 

A PWM of 0 denotes that the pin is alway set to 0V. A PWM of 255 denotes that the pin
is always set to 5V. A PWM of 127 denotes that the pin goes from 0V to 5V for half of
each PWM cycle - on a typical Arduino (such as the Nano used in the project), that cycle is 
about every 2 milliseconds. So a PWM signal of 127 means that it's about 1ms on and 1ms off. 

To slow down the actuator, you would set your PWM signal at a low number - say 10. 
To speed up the movement of the actuator, you would increase the "duty cycle" to something
higher - up to 255. 

There's a good write-up on Arduino's website:
https://docs.arduino.cc/learn/microcontrollers/analog-output/ 

The first two lines only define which pins to use for retracting and extending the flaps.
The third line defines how fast the actuator should go. I don't see any reason to set it
lower than full speed (because the Sonex flap actuator isn't super fast), so 255 it is. 
***************************************************************************/ 
#define RETRACT_PWM_PIN 10
#define EXTEND_PWM_PIN  11
#define ACTUATOR_SPEED  255

/***************************************************************************
  run the setup() function. This section runs one time only, when the Arduino 
  is powered on
***************************************************************************/ 
void setup() {
  // set up serial output
  Serial.begin(115200);


  /*
    set up the button pins. We are initiating each button with a pin number 
    (defined by EXTEND_BUTTON or RETRACT_BUTTON defined above) 
    and specifying that we want to connect the pin to a pull-up resistor. 
    Basically, this adds a 5V signal to the pin at all times until we press a button
    and ground the 5V. When that happens, the Arduino can tell that the button is pressed.
  */ 
  pinMode(EXTEND_BUTTON, INPUT_PULLUP);
  pinMode(RETRACT_BUTTON, INPUT_PULLUP);


  /*
   Set up the display. First, configure the correct type and I2C address (0x3c)
   Next, clear it the screen (the library displays an Adafruit logo by default).
   If you clearDisplay() immediately (like we're doing here), it doesn't appear.
   Finally, set the rotation to 90 degrees - we want to use it in portrait mode
   by using display.setRotation(1) -  you could also set it upside down using 
   display.setRotation(3), but I haven't tested that - good luck if you choose to
   do so. :)
  */ 
  if(!display.begin(SSD1306_SWITCHCAPVCC, SCREEN_ADDRESS)) {
    if (SERIAL_OUTPUT) { Serial.println(F("SSD1306 allocation failed")); }
  }
  display.clearDisplay();
  display.setRotation(1);


  /**************************************************************************
   Next, use the drawTitle() function below to put a bar at the top of the 
   screen with text that says "Flaps."  
   
   Then draw lines where the notches should be and finally draw numbers next
   to those lines - the lines and numbers will change depending on your settings 
   in the ANGLES[] array above
  **************************************************************************/
  drawTitle();
  drawReferenceLines();
  drawReferenceValues();


  /**************************************************************************
    Fill the SENSOR_READINGS array using values defined in the ANGLES array - this will set
    "notches" based on sensor readings (0-1023) instead of ANGLES (0-30, for example), which
    allows for better precision when moving the actuator.

    To do this, we use a "for" loop to iterate through our ANGLES array and 
    change each value to a corresponding SENSOR_READINGS value.
  **************************************************************************/
  for (int i = 0; i<NOTCH_COUNT; i++) {
    SENSOR_READINGS[i] = map(ANGLES[i],ANGLES[0],ANGLES[NOTCH_COUNT - 1],FULL_RETRACT_VALUE, FULL_EXTEND_VALUE);
  }


  /**************************************************************************
    Get the current sensor reading to determine where the flaps are currently 
    positioned
  **************************************************************************/
  int SensorReading = getCurrentSensorReading(); 


  /**************************************************************************
    Find the current notch - the getCurrentNotch() function goes through the list of notches 
    to see if the flaps are set at a particular notch using the SensorReading we just grabbed
  **************************************************************************/
  CURRENT_NOTCH = getCurrentNotch();
  if (SERIAL_OUTPUT) { Serial.print("Beginning CURRENT_NOTCH:");Serial.println(CURRENT_NOTCH); delay(1000); }

}
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

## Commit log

2025-09-05 Added .ino file to a similarly named directory (required by Arduino IDE)
2025-09-06 Added actual Flap Actuator readings and code to run the motor driver. Works pretty well!
2025-09-08 Added code to extend/retract flaps by one notch when the corresponding button is pressed. This should make the workload lighter in the cockpit because you can press the button once and expect the fla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
    Untested ... fingers crossed it's correct (or close to it).
    [sonex_flap_controller.ino]
2025-09-10 Fixed a bug after testing ... still need to look at other stuff, but it's improving.
    [sonex_flap_controller.ino]
2025-09-10 Found another bug - still one more, but this is a good place to stop for now.
    [sonex_flap_controller.ino]
2025-09-10 Started adding PCB stuff.
    [ArduinoBoard.kicad_pcb, ArduinoBoard.kicad_sch]
2025-09-10 Updated the KiCad files.
    [ArduinoBoard.kicad_pcb, ArduinoBoard.kicad_sch]
2025-09-11 Updated the PCB file I was working on.
    [ArduinoBoard.kicad_pcb, ArduinoBoard.kicad_sch]
2025-09-11 Removed some old backup PCB files.
2025-09-12 Updated the kicad files some more
    [ArduinoBoard.kicad_pcb, ArduinoBoard.kicad_sch]
2025-09-13 Updated PCB file again.
    [ArduinoBoard.kicad_pcb]
2025-09-15 Had to make some updates after my first prototype PCB. Hopefully this version is correct. :)
    [ArduinoBoard.kicad_pcb, ArduinoBoard.kicad_sch]
2025-09-15 Trying to simplify code and make it match the new PCB hardware.
    Code compiles, but has some logic issues. I'm tired of looking at it
    for today.
    [sonex_flap_controller.ino]
2025-09-16 Added a 0.1uF capacitor and linked the two GND pins on the Arduino. I seem to have overloaded the Arduino when I plugged in the 12V input - probably a surge. The capacitor should condition the circui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
    [ArduinoBoard.kicad_pcb, ArduinoBoard.kicad_sch]
2025-09-16 Learned that adding a capacitor could actually make the surge worse. Changed to a Negative Temperature Coeficient (NTC) Thermistor instead. The thermistor adds resistance when cool and heats up with 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
    [ArduinoBoard.kicad_pcb, ArduinoBoard.kicad_sch]
2025-09-17 Added a bunch of comment blocks to the Arduino code. Found a logic error or two that I saw as I was writing the comment blocks, so I fixed them.
    [sonex_flap_controller.ino]
2025-09-17 Made some pretty significant changes to the PCB layout. Removed the need for a via path to cross over a couple of tracks.
    [ArduinoBoard.kicad_pcb, ArduinoBoard.kicad_sch]
2025-09-18 A couple of small changes to the PCB prior to printing.
    [ArduinoBoard.kicad_pcb]
2025-09-19 Touched up the getCurrentNotch() function. It would sometimes go beyond the bounds of the ANGLES[] array and get a little funky.
    I still need to fix an issue where pressing the extend button stops at 1 degree (still in the first notch of flaps,
    but not to the second notch). It just stops. I can retract back to 0 degrees again, but it won't go farther than
    1 deg right now for some reason.
    [sonex_flap_controller.ino]
2025-09-19 Looks like I got the issue fixed. Seems to be working as expected.
    [sonex_flap_controller.ino]
2025-10-03 Started to make a 3D printable face plate with Solid Edge. Also added another child board (OLED) that allows a hole to be drilled for a 12mm momentary on-off-on switch (rather than buttons) - this up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
    [ArduinoBoard.kicad_pcb, ArduinoBoard.kicad_sch]
2025-10-04 Pushed the Arduino and other components slightly to the right to make a little more room for the switch.
    [ArduinoBoard.kicad_pcb]
2025-10-04 Updated the Solid Edge part file a little bit. Running out of time, so I'm saving my work.
    [ArduinoBoard.kicad_pcb]
2025-10-05 Added a 2x4 (8-pin) connector to the main board which allows it to connect to the motor controller with a ribbon cable.
    [ArduinoBoard.kicad_pcb, ArduinoBoard.kicad_sch]
2025-10-05 A few little updates - I was interrupted, so I can't remember what all I did. Checking in.
    [ArduinoBoard.kicad_pcb]
2025-10-12 Finished Solid Edge models (probably, anyway) including STL files. Updated some of them too. Updated the PCB board files too. I also added a boolean value called SERIAL_OUTPUT that can be switched on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
    [ArduinoBoard.kicad_pcb, FacePlate.stl, Flap Assembly.cfg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]
2025-10-15 Completed quit a few changes: - Arduino code is working very well. Added a TON of comment lines to describe everything that's happening - Updated the 3D models so everything fits together well and ha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
    No updates to the KiCad files - they seem to be fine.
    [FacePlate.stl, Flap Assembly.cfg, MotorDriverMount.stl]
2025-10-16 Fixed a bug where the indicator coasts a little past it's target location. Works really well now.
    [sonex_flap_controller.ino]
2025-10-21 Updated the 3D model files to fit a 2-1/4" panel cutout.
    [ArduinoBoard.kicad_pcb, FacePlate.stl, Flap Assembly.cfg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]
2025-10-21 Fixed an issue with the MainBoardBed.par Solid Edge file.
    [MainBoardBed.stl]
2025-10-22 Added a couple of images for the Read.me file.
2025-10-24 Redesigned the PCB - moved the screw terminals for the switch to the other side of the board and changed to analog GPIO (A2 & A3) rather than Digital. Moved the two screw holes that were toward the f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
    [ArduinoBoard.kicad_pcb, ArduinoBoard.kicad_sch, MainBoardBed.stl]
2025-10-25 A lot of changes to the 3D models to include cable management. I tried several things until I finally just settled on cutting a few oblong holes in the vertical stiffeners for cable ties. I also made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
    [Flap Assembly.cfg, MainBoardBed.stl, MotorDriverMount.stl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]
2025-10-26 Made a few more 3D Model changes. Rotated the motor driver 90 degrees counter clockwise, which puts the wiring out the back of the device rather than off to one side. Going out the side made the wire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
    [MotorDriverMount.stl]
2025-10-28 Hopefully a final update to the 3D models. Will put one together to see if everything fits properly.
    [Flap Assembly.cfg, MainBoardBed.stl, MotorDriverMount.stl]
2025-10-31 Updated the code a little, but mostly added Gerber files that can be used to purchase custom PCBs from one of the many PCB manufacturing companies.
    [ArduinoBoard-B_Courtyard.gbr, ArduinoBoard-B_Cu.gbl, ArduinoBoard-B_Fab.gbr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]
2025-10-31 A couple of very minor code tweaks (mostly comment blocks)
2025-12-03 Updated the 3D models: - Made the MainBoardBed model a little taller and stronger (added a stringer). - Also made it possible to rotate the MotorDriverMount model upward for a shallower panel - Added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
    Exported STL files for all models.
    [45DegMotorBoardBedSpacer.stl, 90DegMotorBoardBedSpacer.stl, FacePlate.stl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]
2026-03-13 Fixed a gerber file issue reported by Jon Parnaby. He noted that a lot of the through holes in the PCBs he ordered from JLCPCB were too small (for Arduino and other components). I grew the holes from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
    Also updated the printable PDFs for PCB transfer paper (e.g. reversed, underside, copper-only).
    [ArduinoBoard-B_Cu.gbl, ArduinoBoard-B_Fab.gbr, ArduinoBoard-B_Mask.gbs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]
2026-04-25 Updated the MainBoardBed part to improve printability (made a flat(ish) bottom).
    [Flap Assembly.cfg]
2026-04-25 Updated a couple of measurements on the user.1 layer.
    [ArduinoBoard.kicad_pcb]
2026-04-25 Completed changes to the MainBoardBed.par and exported to STL as well.
    [MainBoardBed.stl]

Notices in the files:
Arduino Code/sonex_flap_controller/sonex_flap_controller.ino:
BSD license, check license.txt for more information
